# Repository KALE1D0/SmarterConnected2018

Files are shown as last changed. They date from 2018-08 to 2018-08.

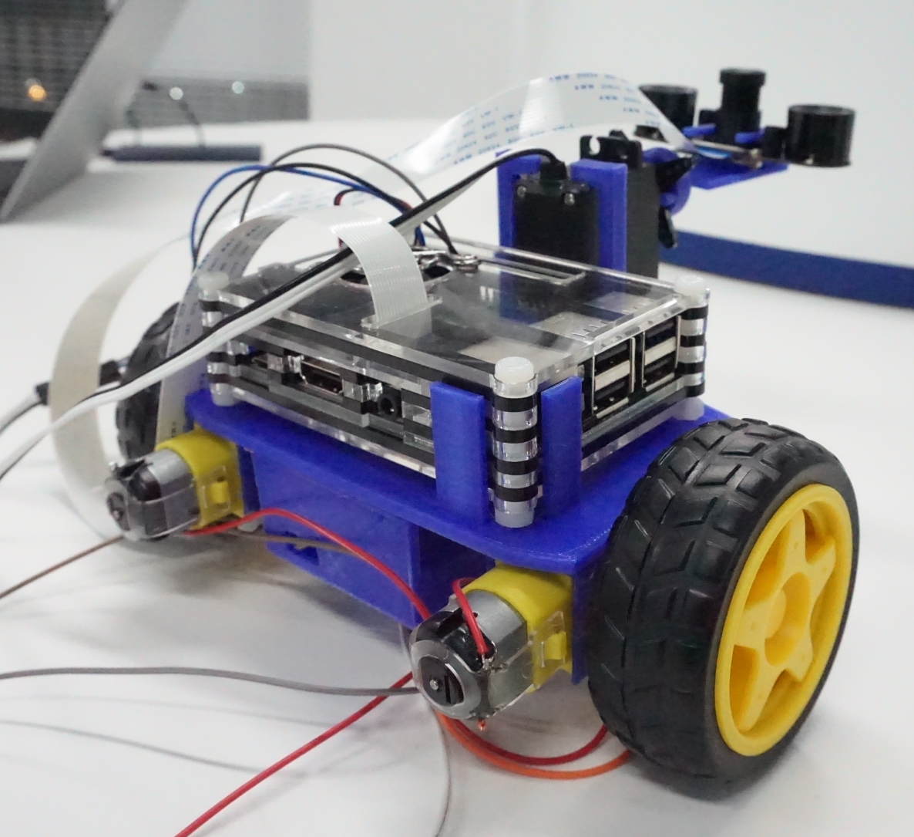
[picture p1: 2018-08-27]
photo/MKII/4.jpg

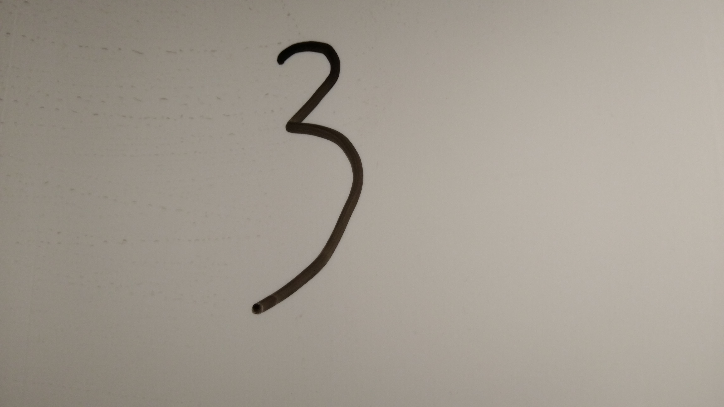
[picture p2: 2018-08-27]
src/ros_packs/znhl/picture/3.jpg

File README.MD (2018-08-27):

# What is this
A personal project cooperating with @bechanged233 and @reclugjw for Smarter-Connected-2018.

# Directories
sample\\: Test samples for defect/crack detecting.

doc\\: Reports and scripts for this project.

model\\: Solidworks model files of structure.

slide\\: PPTs for the report.

src\\: Source Codes. [src\ros_packs\send_pic] should be in the RasPi.

photo\\: Photos of our product.

# License
Copyleft.

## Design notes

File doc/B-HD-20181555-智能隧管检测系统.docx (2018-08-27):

第十四届“博创杯”全国大学生嵌入式设计大赛

作品设计报告

智能隧管检测系统

Intelligent tunnel detection system

设

计

报

告

队伍编号：

参赛学校：

作 者：

指导教师：

组 别：■本科组 □高职组

未找到目录项。

摘 要

目前的交通道路有朝着地下化、隧道化方向发展的趋势，地铁隧道也将成为未来城市交通的主要发展方向。同时各类城市管道的长度也在逐年上升。对于隧道、管道等类似的封闭环境，现有的缺陷检测方法成本高昂，形式单一，有着工序繁琐、耗时极长等弊端，不利于城市交通与管线系统的可持续发展。

因此，本项目设计了一套以图像识别与超声波测距为主要传感器，基于STM32与树莓派的小型智能化隧管缺陷检测系统，并通过ROS实现了设备与上位机的通信。我们在把对管道、隧道的缺陷检测统一化的同时，设计了一套离线作业系统，并力求在满足精确、高效的同时，将成本控制在合理的范围之内，进而使得其能够被大规模投放使用，因而具有很强的实用性与可推广性。

同时，本项目也提出了一种基于超声波传感器与摄像头相配合的小直径隧管彩色三维重构方法，并在进行数学推导与可行性论证之后，使用程序模拟实现了三维重构的效果。

关键词：智能交通、图像识别、ROS、超声波测距、三维重构

Abstract

Nowadays, the traffics system are moving toward undergroundization and tunnelling. Subways are becoming the main stream of the development of future urban transportation. At the same time, the length of various types of urban pipelines has also increased year by year. For tunnels, pipelines and similar closed environments, the existing defect detection methods are expensive, not various, and have drawbacks such as cumbersome procedures, extremely long time-consuming, and are not conducive to the sustainable development of urban traffic and pipeline systems.

Therefore, this project designed a set of small sensor tunnel detection system based on STM32 and Raspberry Pi with image recognition and ultrasonic ranging as the main sensors, and achieved communication between the device and host computer through ROS. While we unify the detection of defects in pipelines and tunnels, we designed an online operation system, and strived to control the cost within a reasonable range while satisfying the accuracy and efficiency, and in turn making it possible to be put into large-scales, so it has a strong practicality and scalability.

At the same time, a colorful 3D reconstruction method for small-diameter tunnel tubes based on ultrasonic sensors and cameras is also proposed in this project. After mathematical derivation and feasibility demonstration, the effects of 3D reconstruction are achieved using program simulation.

Key words: Intelligent traffic, image recognition, ROS, ultrasonic ranging, 3D reconstruction

第1章 绪 论

## 1.1 视觉识别技术

视觉检测系统是用相机代替人眼睛去完成识别.测量.定位等功能。一般视觉检测系统由相机、镜头、光源组合合成，可以代替人工完成条码字符 (https://baike.baidu.com/item/%E6%9D%A1%E7%A0%81%E5%AD%97%E7%AC%A6)、裂痕、包装、表面图层是否完整、凹陷等检测，使用视觉检测系统能有效的提高生产流水线的检测速度和精度，大大提高产量和质量，降低人工成本，同时防止因为人眼疲劳而产生的误判。

## 1.2 三维重构技术

三维重建，指的是通过摄像机获取场景物体的数据图像，并对此图像进行分析处理，再结合计算机视觉知识推导出现实环境中物体的三维信息。

根据重建的稀疏程度不同，可以分为以下以下几类：

稀疏重建：

通常是重建一些图像特征点的深度，这个在基于特征的视觉SLAM里比较常见，得到的特征点的深度可以用来计算相机位姿。稀疏重建在实际应用，比如检测，避障，不能满足需求。

半稠密重建：

通常是重建图像纹理或梯度比较明显的区域，这些区域特征比较鲜明。半稠密重建在直接法视觉SLAM里比较常见。重建的三维点云相对稠密，可以满足部分应用需求。

稠密重建：

稠密重建是对整个图像或者图像中的绝大部分像素进行重建。与稀疏、半稠密相比，稠密重建对场景的三维信息理解更全面，更能符合应用需求。但是，由于要重建的点云数量太多，相对耗时。本项目所设计的三维重构方法属于半稠密重建。根据重建的实时性不同，可以分为离线重建和在线重建。

离线重建：

比如 SFM(运动恢复结构)技术，此技术根据在一段时间内获得的连续图像来重建一个三维环境。

在线重建：在线重建可以分为渐进式重建和直接式重建。在线重建或多或少都和VO或者(SLAM)有联系，因为重建的时候需要相机的位姿。我们所设计的是离线重建

## 1.3 ROS机器人系统

ROS---(Robot Operating System）是一个机器人软件平台，它能为异质计算机集群提供类似操作系统的功能。ROS提供一些标准操作系统服务，例如硬件抽象，底层设备控制，常用功能实现，进程间消息以及数据包管理。ROS是基于一种图状架构，从而不同节点的进程能接受，发布，聚合各种信息（例如传感，控制，状态，规划等等）。ROS可以分成两层，低层是上面描述的操作系统层，高层则是广大用户群贡献的实现不同功能的各种软件包，例如定位绘图，行动规划，感知，模拟等等。ROS的核心是节点。节点是一小段用Python或C++写成的程序，用来执行某个相对简单的任务或进程。多个节点之间互相传递信息，并可以独立控制启动或终止。某一节点可以面向其它节点针对特定标题发布信息或提供服务。

## 1.4 隧道检测现状

随着国家经济的不断发展，为了满足日益增长的通行和城市发展需求，各类管网在近十年不断增长。据统计，截止到2017年，仅国内地铁管网长度就已经达到了世界前列，上海与北京更分列第一第二。如此大规模的交通管网带来的不仅只有方便，也带来了大量的附加问题。其中，管道维护是目前很多部门关注的重点。以地铁管道为例，现有的管道检测技术无法准确检测出管道裂缝，更无法判断出管道损坏的位置的影响程度，目前大多使用人工肉眼检测，且管道条件复杂，人工检测危险重重，国内外多次出现管道工人意外身亡事故。

第2章 系统方案

## 2.1 系统总体设计

小车端与PC主控端通过蓝牙和WIFI进行连接，开发板与PC主控端通过USB有线连接，传感器与驱动部分用串口进行连接。最终通过ROS控制各模块并且进行数据传输，从而实现预期功能。

## 2.2 系统工作流程

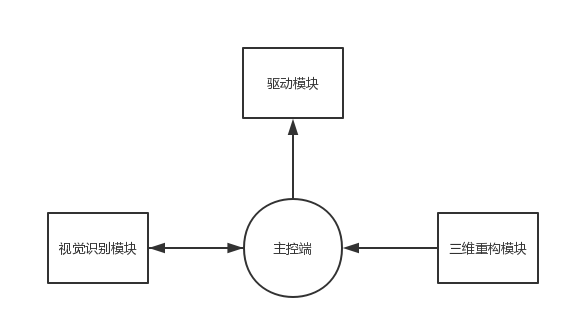
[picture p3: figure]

第3章 功能与指标

## 3.1 硬件模块

3.1.1 机械结构
1. 相机底座
相机底座采用了夹持的设计思想，通过伸出的两个臂状长方体将相机紧紧地夹在底板上，使得镜头能够在整个平面内360度旋转；同时这两个“手臂”不会影响到边上的光敏电阻与红外补光灯，使得整个设备在阴暗的环境下也能正常、平稳地工作。

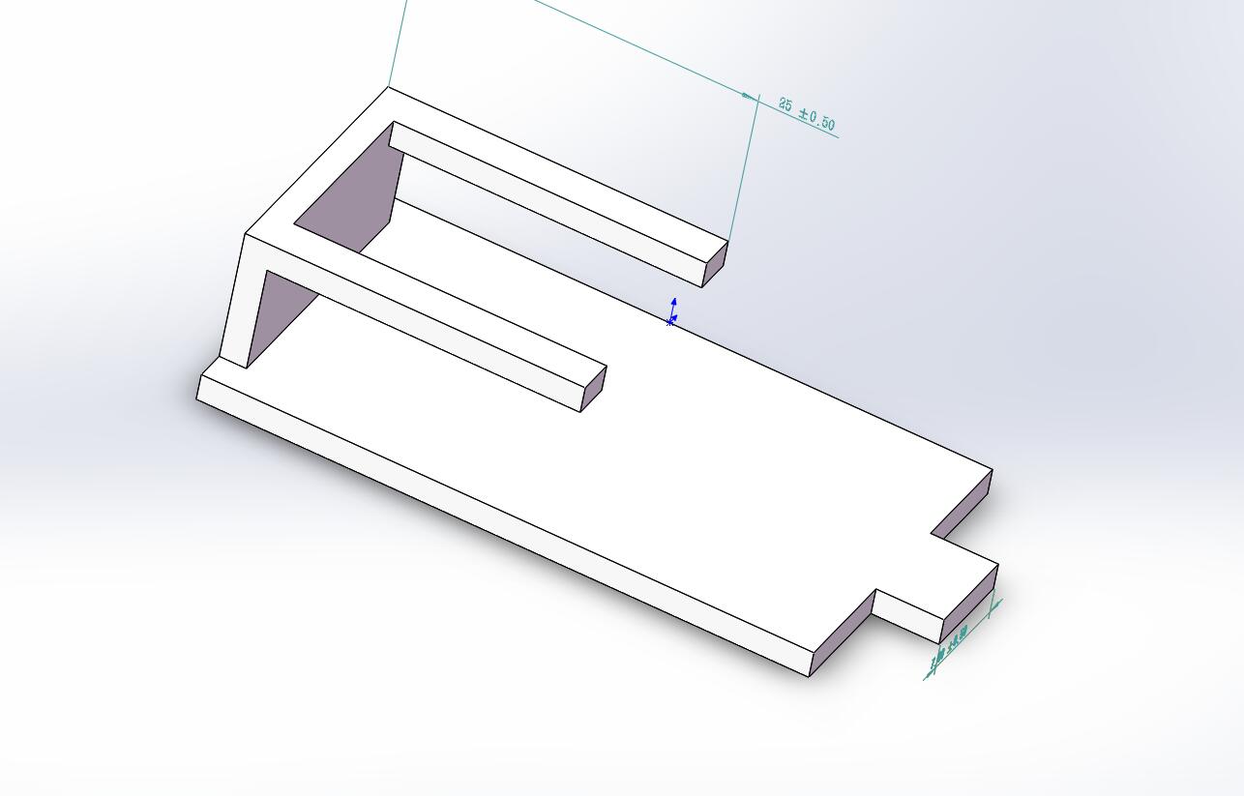
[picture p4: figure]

相机底座

2. 前部支架

前部支架为支撑车辆前部的舵机与摄像头而设计，其符合力学原理的结构与定制的万向轮插槽使得整个车辆能自由、灵活地进行转向，并能够防止车体质量的不平衡所导致的倾斜与晃动，使得车辆能够在一般环境下平稳地前进。

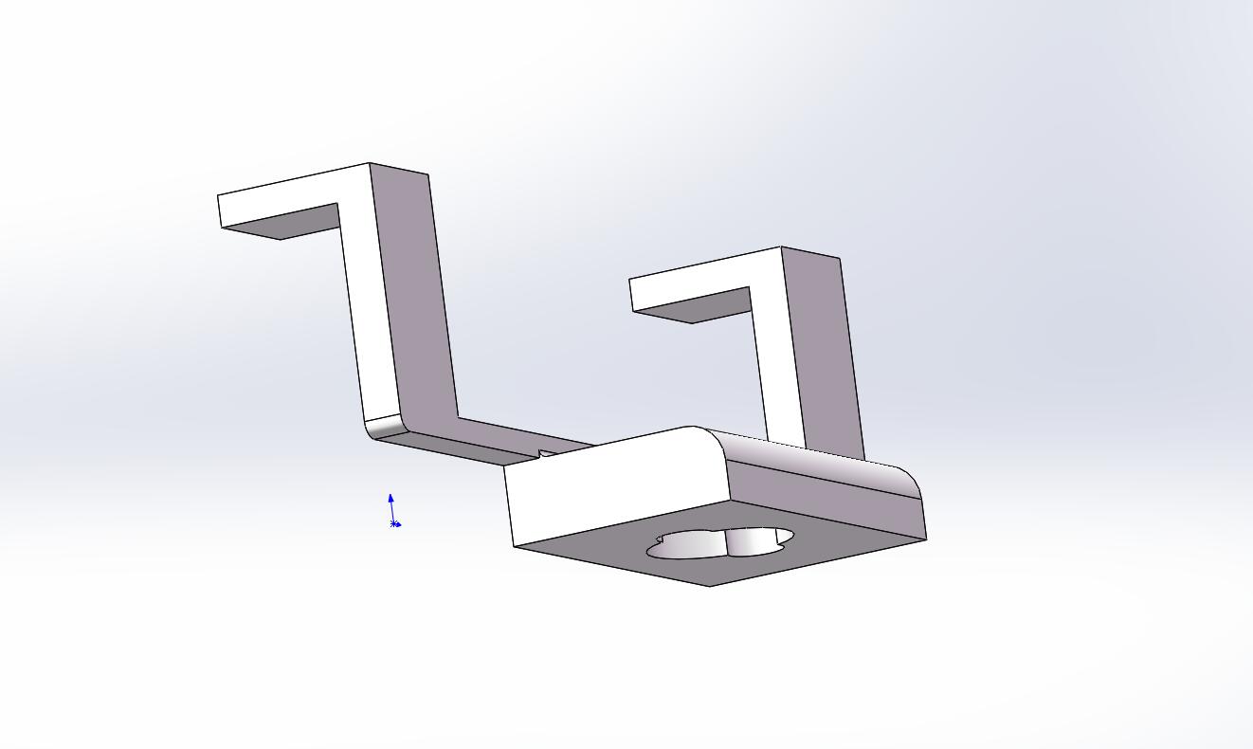
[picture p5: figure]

前置支架

3. 驱动电机支架

驱动电机支架专为直流减速电机而设计，其能够良好地对电机进行保护，并将电机的核心部件与外部环境隔离开来，有效防止电机过载等意外情况的发生。

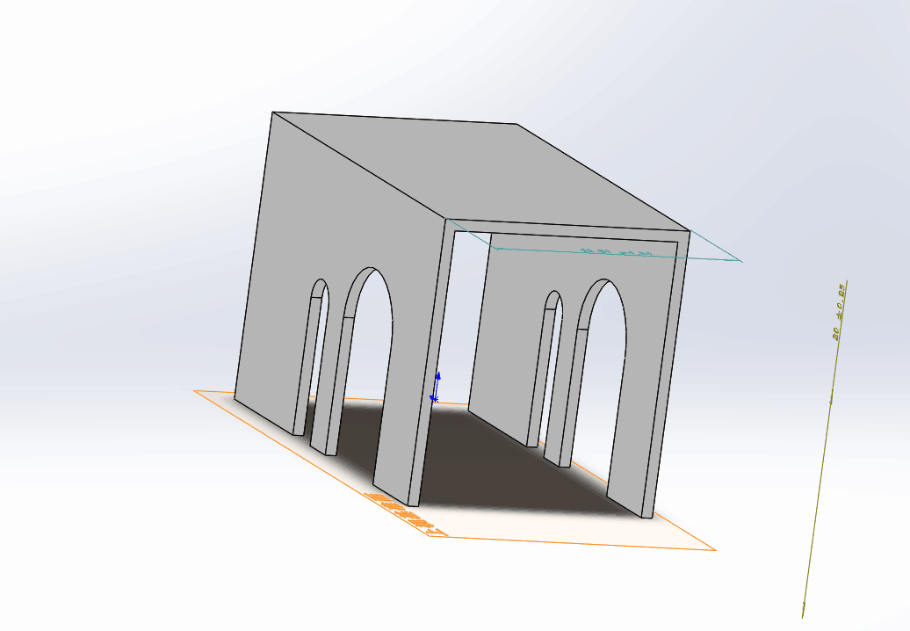
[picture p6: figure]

电机支架

4. 主控板

主控板是整个设备设计的核心，在它之下，连接了驱动电机支架与控制底座，在它中央的凹槽则是用于放置5V树莓派专用供电电池，而用保护壳进行保护的树莓派运算板则直接被放置在供电电池之上，被五个设计精巧的挡板紧紧地扣住；而在其前方，则是连接了舵机支架，进而与摄像头设备相连，使得整个系统在保证功能性的基础上将结构优化到了极致。

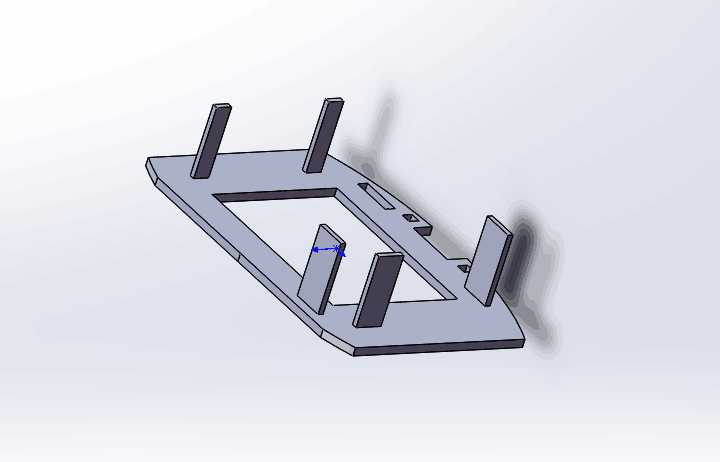
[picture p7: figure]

主控板

5. 舵机支架

舵机支架采用简单的支撑型设计，在其底部的两个圆柱向前伸出，平稳地拖住了质量较大的电机，而在支架的正下方的两个正方形凸口，则转为与主控板进行连接而设计，其能够牢牢地嵌入主控板之中，进而使得舵机能进行良好、可靠的运作。

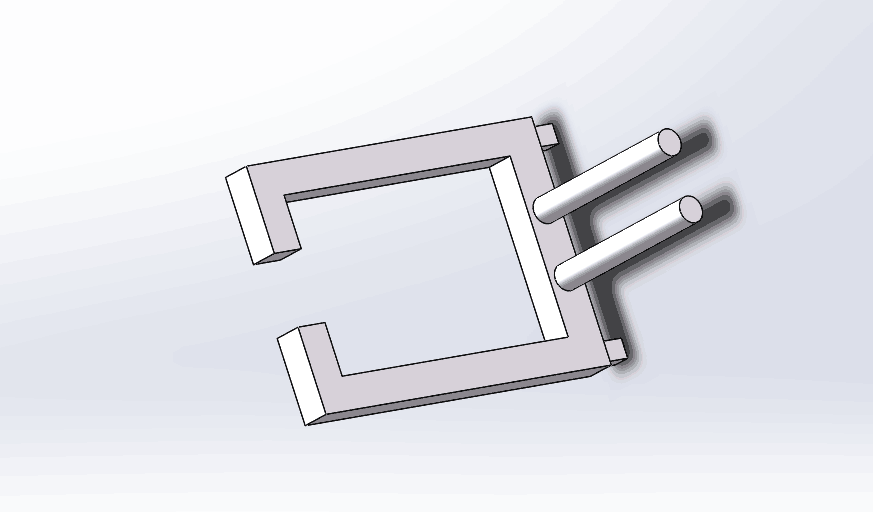
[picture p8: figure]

舵机支架

3.1.2 视觉识别硬件结构

1. Rpi Camera

我们采用带自感应式红外补光的RPiCamera摄像头。当环境光较弱时，其两侧的红外补光灯会自动开启，使得机器人能在各种不同光照环境下工作。RpiCamera的数据流可直接通过树莓派发送到上位机，从而实现实时检测的功能。

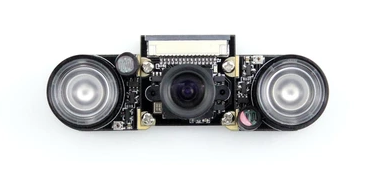
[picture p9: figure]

Rpi Camera

2. Raspberry

我们采用RaspberryPi3B来对摄像头获得的图形进行预处理与储存。RaspberryPi3B是基于ARM内核的性能强大的开源硬件，我们在其上安装了最新的轻量级操作系统Raspbian，使得我们能够非常容易地与其交互。

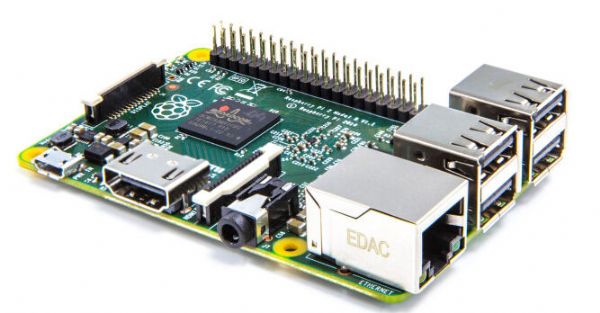
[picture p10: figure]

Raspberry Pi 3B

3.1.3. 三维重构硬件结构

我们设计的三维重构系统需要一个类似于激光雷达的传感器。我们的方案是将超声波与姿态传感器被捆绑在一起，挂载到可以三百六十度旋转的舵机上。同时，我们使用低功耗蓝牙模块来实现短距离的数据传输，使树莓派能够收到来自超声波传感器的数据。

1. 九轴姿态传感器

我们准备使用MPU9250模块来获取超声波雷达的位姿。MPU9250能够实时测量其三轴上的加速度、角加速度与地磁角，从而精确地估计出雷达的姿态角。

MPU9250

2. 超声波模块

为了提升距离的准确性，我们选用了US-100超声波传感器。US-100有着方向角较小、精度较大的特点，其探测范围可达2cm-450cm，而误差仅有0.3cm±1%，因而可以较好地检测出设备到管道内壁的距离。

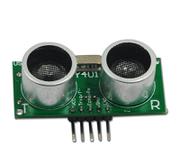
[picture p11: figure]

US-100

3.2.4. 小车运动模块硬件结构

1. STMF103C8T6

我们采用STM32F103C8T6最小系统板。STM32是基于ARM® Cortex® M 处理器内核的 32位闪存微控制器，集高性能、高实时性、数字信号处理、低功耗于一身，基于行业标准，具有大量工具和软件可供选择，是本项目控制部件的的理想选择。

STM32F103C8T6

2. 减速电机及橡胶轮

我们采用了通用减速直流电机与60mm直径的橡胶轮，其具有强磁、带抗干扰等特性。我们会为其提供5V直流供电，使得机器人能在较平缓的隧道内稳步前行。

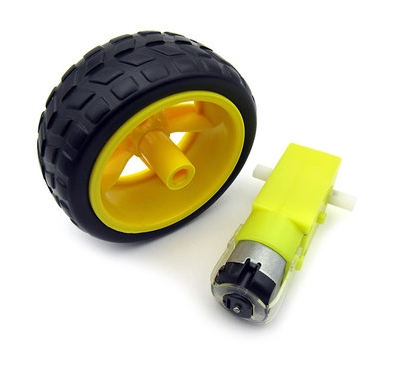
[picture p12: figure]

直流减速电机与轮胎

## 3.2 软件模块

3.2.1. 视觉识别算法

我们采用了基于视觉识别技术的缺陷检测算法，其原理是不断去除图像上的噪声，仅仅留下我们需要的特征也即裂缝等缺陷的轮廓。

1. 噪点消除

由于管道内复杂的环境与摄像头本身的物理特性，我们得到的初始图像数据往往带有较多噪点，这些噪点会影响成像的质量，进而干扰我们对缺陷特征的判断。因此，获取图像后我们首先要做的是使用滤波算法对图像去噪。

常用的滤波算法有均值滤波、高斯滤波、中值滤波等。经过我们多次尝试，在模拟的隧管环境下高斯滤波的去噪效果最好。除此之外它也有着较好的平滑化效果。

高斯滤波是一种线性平滑滤波，适用于消除高斯噪声，广泛应用于图像处理的减噪过程。通俗的说，高斯滤波就是对整幅图像进行加权平均 (https://baike.baidu.com/item/%E5%8A%A0%E6%9D%83%E5%B9%B3%E5%9D%87)的过程，每一个像素点的值，都由其本身和邻域内的其他像素值经过加权平均后得到。高斯滤波的具体操作是：用一个模板（或称卷积、掩模）扫描图像中的每一个像素，用模板确定的邻域内像素的加权平均灰度值去替代模板中心像素点的值。

高斯滤波一般有两种实现方式，一是用离散化窗口滑窗卷积，另一种通过傅里叶变换 (https://baike.baidu.com/item/%E5%82%85%E9%87%8C%E5%8F%B6%E5%8F%98%E6%8D%A2)。而只有当离散化的窗口非常大，用滑窗计算量非常大（即使用可分离滤波器的实现）的情况下，可能会考虑基于傅里叶变化的实现方法。故在这里我们使用离散化窗口滑窗卷积。

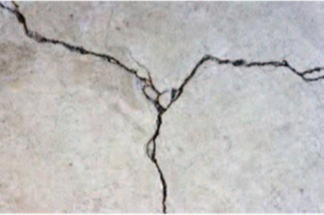
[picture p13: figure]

高斯滤波效果演示一

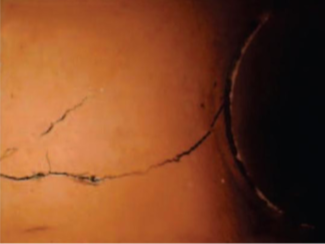
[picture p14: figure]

高斯滤波效果演示二

2. 缺陷检测：边缘检测

去除噪点之后，我们就可以对图像进行处理了。我们选用的主要缺陷检测手段是边缘检测算法。常用的边缘检测算法有Roberts算子，Sobel算子，Canny算子，形态学算子等等。

在对多种算子进行测试后，我们发现使用Canny算子进行腐蚀与膨胀运算后可以较好的检测出条状的裂缝，并且团状的潜在危险因素也能被呈现出来。

Canny算子在进行简单除噪后开始寻找图像中的亮度梯度，图像中的边缘可能会指向不同的方向，所以 Canny 算法使用 4 个 mask 检测水平、垂直以及对角线方向的边缘。原始图像与每个 mask 所作的卷积 (https://baike.baidu.com/item/%E5%8D%B7%E7%A7%AF)都存储起来。对于每个点我们都标识在这个点上的最大值以及生成的边缘的方向。这样我们就从原始图像生成了图像中每个点亮度梯度图以及亮度梯度的方向。由于较高的亮度梯度比较有可能是边缘，但是没有一个确切的值来限定多大的亮度梯度是边缘多大，所以 Canny 使用了滞后 (https://baike.baidu.com/item/%E6%BB%9E%E5%90%8E)阈值。

滞后阈值需要两个阈值——高阈值与低阈值。假设图像中的重要边缘都是连续的曲线，这样我们就可以跟踪给定曲线中模糊的部分，并且避免将没有组成曲线的噪声像素当成边缘。所以我们从一个较大的阈值开始，这将标识出我们比较确信的真实边缘，使用前面导出的方向信息，我们从这些真正的边缘开始在图像中跟踪整个的边缘。在跟踪的时候，我们使用一个较小的阈值，这样就可以跟踪曲线的模糊部分直到我们回到起点。

一旦这个过程完成，我们就得到了一个二值图像，每点表示是否是一个边缘点。进而获得我们所需要的边缘图像。

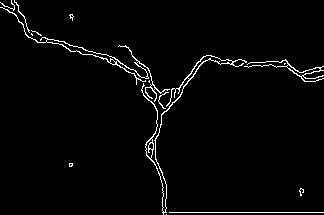
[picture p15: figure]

缺陷检测效果演示一

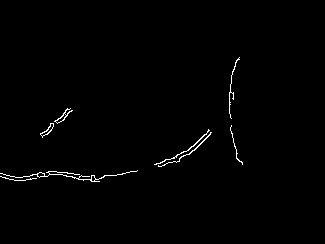
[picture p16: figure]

缺陷检测效果演示二

3. 缺陷检测：阈值分割

边缘检测算法之外，还有一类算法也能够较有效地检测出隧管壁上的缺陷，那就是阈值分割算法。阈值分割指以某一阈值为分界线将一幅图像按照灰度值转化成黑白二值图。我们将经过预处理的图像按灰度值分割成两个点集，当被分割成的两个点集之间方差最大时，该灰度值就是将图像二值化所需要的阈值。此处我们所采用的是一种自适应阈值分割算法：使用遗传算法求解的大津法(OTSU)。该方法耗时较长，可用于图像的离线处理过程之中。

使用遗传算法求解的大津法效果演示

其具体代码实现如下：

1. import cv2
2. import numpy as np
3. from matplotlib import pyplot as plt
4. import random
5. import matplotlib.patches as mpatches
6. import scipy.ndimage as ndi
7. from skimage import morphology,filters
10. imag = cv2.imread("D:test4.png")
11. cv2.imshow("orignal",imag)
13. gray = cv2.cvtColor(imag, cv2.COLOR_BGR2GRAY)
14. cv2.imshow("gray",gray)
17. img = cv2.GaussianBlur(gray,(3,3),0)
18. cv2.imshow("Gau",img)
21. canny = cv2.Canny(img, 50, 150)
22. cv2.imshow("canny",canny)
24. kernel = cv2.getStructuringElement(cv2.MORPH_RECT,(3, 3))
25. erosion = cv2.erode(img,kernel,iterations = 1)
26. dilation = cv2.dilate(erosion,kernel,iterations = 1)
27. cv2.imshow("deliation",dilation)
29. canny = cv2.Canny(dilation, 50, 150)
30. cv2.imshow("canny",canny)
31. def expand(k, m):
32. for i in list(range(len(k))):
33. k[i] = k[i][:2] + '0'*(8*m+2 - len(k[i])) + k[i][2:len(k[i])]
34. return k
37. def Hist(image):
38. a=[0]*256
39. h=image.shape[0]
40. w=image.shape[1]
41. MN=h*w
42. average=0.0
43. for i in list(range(w)):
44. for j in list(range(h)):
45. pixel=int(image[j][i])
46. a[pixel]=a[pixel]+1
47. for i in list(range(256)):
48. a[i]=a[i]/float(MN)
49. average=average+a[i]*i
50. return a, average
54. def getTh(seed, m):
55. th = [0, 256]
56. seedInt = int(seed, 2)
57. for i in list(range(0, m)):
58. tmp = seedInt & 255
59. if tmp != 0:
60. th.append(tmp)
61. seedInt = seedInt >> 8
62. th.sort()
63. return th
67. def fitness(seed, p, average, m):
68. Var = [0.0] * len(seed)
69. g_muT = 0.0
71. for i in list(range(256)):
72. g_muT = g_muT + i * p[i]
74. for i in list(range(len(seed))):
75. th = getTh(seed[i], m)
76. for j in list(range(len(th)-1)):
77. w = [0.0] * (len(th)-1)
78. muT = [0.0] * (len(th)-1)
79. mu = [0.0] * (len(th)-1)
80. for k in list(range(th[j], th[j+1])):
81. w[j] = w[j] + p[k]
82. muT[j] = muT[j] + + p[k] * k
83. if w[j] > 0:
84. mu[j] = muT[j] / w[j]
85. Var[i] = Var[i] + w[j] * pow(mu[j] - g_muT, 2)
86. return Var
90. def wheel_selection(seed, Var):
91. var = [0.0]*len(Var)
92. s = 0.0
93. n = ['']*len(seed)
94. sumV = sum(Var)
95. for i in list(range(len(Var))):
96. var[i] = Var[i]/sumV
97. for i in list(range(1, len(Var))):
98. var[i] = var[i] + var[i-1]
99. for i in list(range(len(seed))):
100. s = random.random()
101. for j in list(range(len(var))):
102. if s <= var[j]:
103. n[i] = seed[j]
104. return n
108. def Cross(Next, m):
109. for i in list(range(0, len(Next) - 1, 2)):
110. if random.random() < 0.7:
111. if m > 2:
112. tmp = Next[i][10:]
113. Next[i] = Next[i][:10] + Next[i+1][10:]
114. Next[i+1] = Next[i+1][:10] + tmp
115. else:
116. tmp = Next[i][6:]
117. Next[i] = Next[i][:6] + Next[i+1][6:]
118. Next[i+1] = Next[i+1][:6] + tmp
119. return Next
123. def Variation(Next):
124. for i in list(range(len(Next))):
125. if random.random()<0.06:
126. Next[i]=bin(int(Next[i],2)+2)
127. return Next
131. def genetic_thres(image, k, m):
132. th = image
133. for i in list(range(image.shape[0])):
134. for j in list(range(image.shape[1])):
135. for t in list(range(1, len(k)-1)):
136. if k[t-1] <= image[i][j] < k[t]:
137. th[i][j] = int(k[t-1])
138. return th
139. image=canny
140. m = 3
141. items_x = list(range(0, image.shape[0]))
142. items_y = list(range(0, image.shape[1]))
143. random.shuffle(items_x)
144. random.shuffle(items_y)
145. x = items_x[0:20*m]
146. y = items_y[0:20*m]
147. seed = []
148. Var = 0.0
149. times = 0
150. k = 0
151. P, average = Hist(image)
152. for i in list(range(0, 20)):
153. code = int(0)
154. for j in list(range(0, m)):
155. code = code + gray[x[i*j]][y[i*j]] << j*8
156. seed.append(bin(code))
158. while times < 2000:
159. Var = fitness(seed, P, average, m)
160. Next = wheel_selection(seed, Var)
161. Next = Cross(Next, m)
162. Next = expand(Variation(Next), m)
163. seed = Next
164. times = times + 1
166. for j in list(range(len(Var))):
167. if Var[j] == max(Var):
168. k = getTh(Next[j], m)
169. print (k)
171. plt.subplot(131), plt.imshow(image, "gray")
172. plt.title("source image"), plt.xticks([]), plt.yticks([])
175. plt.subplot(132), plt.hist(image.ravel(), 256)
176. plt.title("Histogram"), plt.xticks([]), plt.yticks([])
179. th1 = genetic_thres(image, k, m)
180. plt.subplot(133), plt.imshow(th1, "gray")
181. titleName = ''
182. for i in list(range(1, len(k)-1)):
183. titleName = titleName + str(k[i]) + ', '
184. titleName = titleName[:len(titleName)-2]
185. plt.title("threshold is " + titleName), plt.xticks([]), plt.yticks([])
186. plt.show()
189. cv2.waitKey(0)

3.2.2 三维重构算法

1. 倾角估测

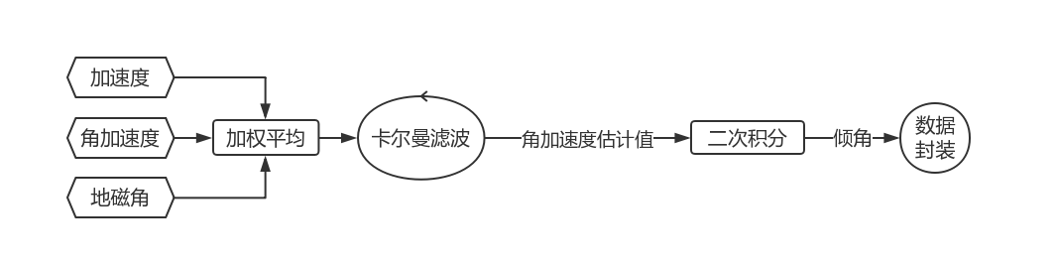
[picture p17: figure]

倾角估计算法原理

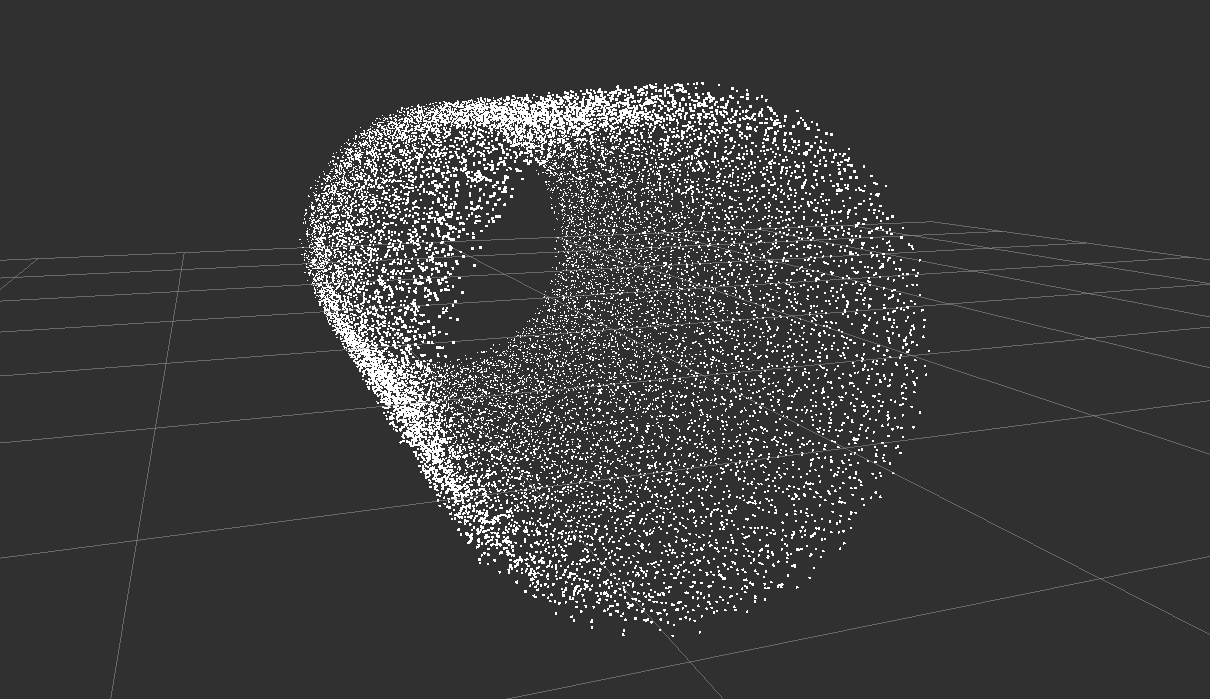
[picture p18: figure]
无标题_看图王

程序模拟的倾角估计生成的点云效果图

2. 点云染色

我们使用摄像头与超声波传感器之间的距离值L与点云到超声波传感器的距离D进行三角运算后可估算出物体在摄像机视场内与摄像机法线的夹角α，随后将其正切值与摄像机视角正切值的比例代入计算即可获得其在摄像机所获得的像素图上的具体位置，从而得到该点的像素值。

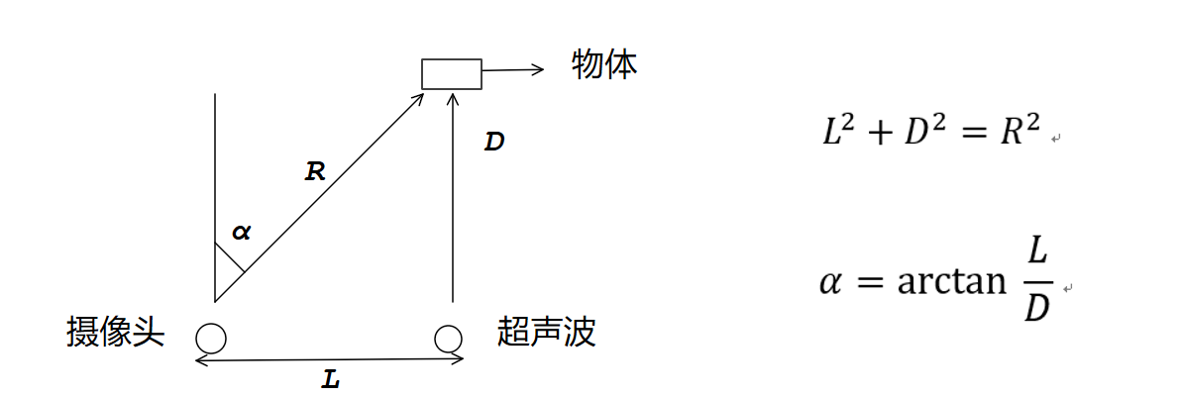
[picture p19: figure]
无标题2_看图王
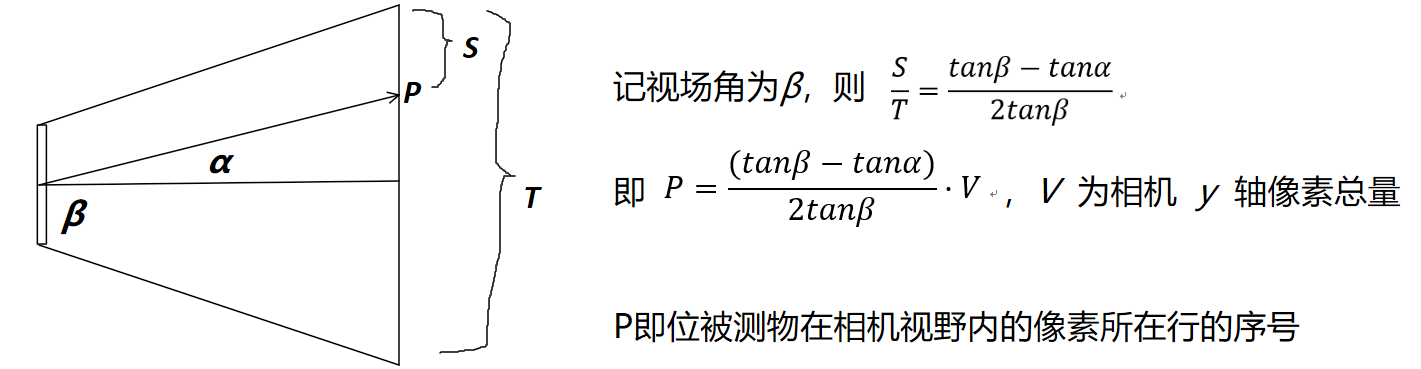
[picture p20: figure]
无标题2_看图王

点云染色算法原理

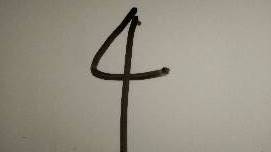
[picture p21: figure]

管道内壁数字图案实拍照片

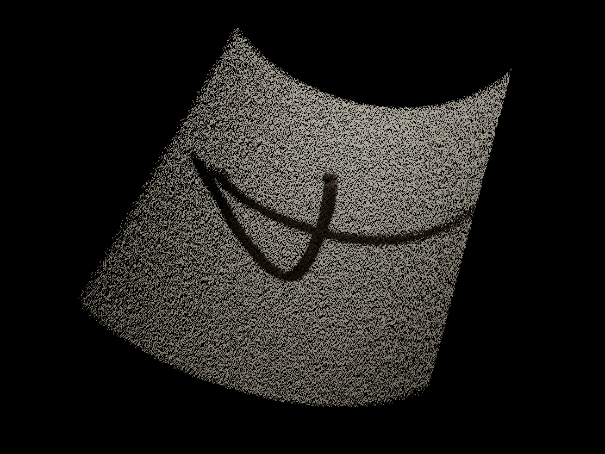
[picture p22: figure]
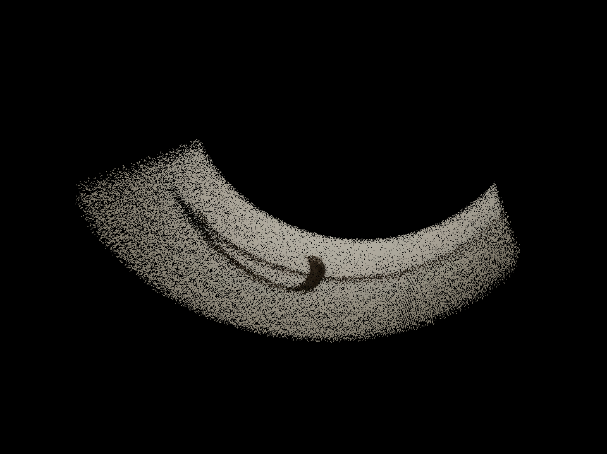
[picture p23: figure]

点云染色效果

其具体实现代码如下：

1. #include <pcl/visualization/cloud_viewer.h>
2. #include <iostream>
3. #include <pcl/io/io.h>
4. #include <pcl/io/pcd_io.h>
5. #include <opencv2/opencv.hpp>
7. using namespace std;
9. int user_data;
10. const double u0 = 319.52883;
11. const double v0 = 271.61749;
12. const double fx = 528.57523;
13. const double fy = 527.57387;
16. void viewerOneOff(pcl::visualization::PCLVisualizer& viewer)
17. {
18. viewer.setBackgroundColor(0.0, 0.0, 0.0);
19. }
21. int main()
22. {
23. pcl::PointCloud<pcl::PointXYZRGB> cloud_a;
24. pcl::PointCloud<pcl::PointXYZRGB>::Ptr cloud(new pcl::PointCloud<pcl::PointXYZRGB>);
26. cv::Mat color = cv::imread("rgb.jpg");
27. cv::Mat depth1 = cv::imread("depth.png");
29. cv::Size dsize = cv::Size(color.cols, color.rows);
30. cv::Mat depth = cv::Mat(dsize, CV_8UC3);
31. resize(depth1,depth,dsize);
33. int rowNumber = color.rows;
34. int colNumber = color.cols;
36. cloud_a.height = rowNumber;
37. cloud_a.width = colNumber;
38. cloud_a.points.resize(cloud_a.width * cloud_a.height);
40. for (unsigned int u = 0; u < rowNumber; ++u)
41. {
42. for (unsigned int v = 0; v < colNumber; ++v)
43. {
44. unsigned int num = u*colNumber + v;
45. double Xw = 0, Yw = 0, Zw = 0;
47. //Zw = ((double)depth.at<uchar>(u, v)) / 255.0 * 10001.0;
48. //Xw = (u - u0) * Zw / fx;
49. //Yw = (v - v0) * Zw / fy;
50. Zw = ((double)depth.at<uchar>(u, v));
51. Xw = u;
52. Yw = v;
54. cloud_a.points[num].b = color.at<cv::Vec3b>(u, v)[0];
55. cloud_a.points[num].g = color.at<cv::Vec3b>(u, v)[1];
56. cloud_a.points[num].r = color.at<cv::Vec3b>(u, v)[2];
58. cloud_a.points[num].x = Xw;
59. cloud_a.points[num].y = Yw;
60. cloud_a.points[num].z = Zw;
61. }
62. }
64. *cloud = cloud_a;
66. pcl::visualization::CloudViewer viewer("Cloud Viewer");/*
67. viewer.showCloud(cloud);
69. viewer.runOnVisualizationThreadOnce(viewerOneOff);
71. while (!viewer.wasStopped())
72. {
73. user_data = 9;
74. }
75. */
76. return 0;
77. }

3. 三维重构

通过将获得的彩色点云数据打包封装成ROS消息发布到ROS系统里，让RVIZ对其进行监听与处理，即可在RVIZ中看到彩色的三维重构结果。

其具体实现代码如下：

1. #include <ros/ros.h>
2. #include <pcl/point_cloud.h>
3. #include <pcl_conversions/pcl_conversions.h>
4. #include <sensor_msgs/PointCloud2.h>
5. #include <bits/stdc++.h>
7. pcl::PointCloud<pcl::PointXYZ> gen_pipe(int round, int layer, int length) {
8. pcl::PointCloud<pcl::PointXYZ> cloud;
9. cloud.width = round * layer;
10. cloud.height = 1;
11. cloud.points.resize(cloud.width * cloud.height);
13. for (size_t i = 0; i < cloud.points.size (); ++i)
14. {
15. double theta = (double)(i % round) / round * 2 * acos(-1.0);
16. cloud.points[i].x = (double)(i / round + 1) / layer * length;
17. cloud.points[i].y = cos(theta) * (1 + rand () / (RAND_MAX + 1.0f) / 7);
18. cloud.points[i].z = sin(theta) * (1 + rand () / (RAND_MAX + 1.0f) / 7);
19. }
20. return cloud;
21. }
23. main (int argc, char **argv)
24. {
25. ros::init (argc, argv, "pcl_create");
27. ros::NodeHandle nh;
28. ros::Publisher pcl_pub = nh.advertise<sensor_msgs::PointCloud2> ("pcl_output", 1);
29. //pcl::PointCloud<pcl::PointXYZ> cloud = gen_circle();
30. sensor_msgs::PointCloud2 output;
31. //Convert the cloud to ROS message
32. ros::Rate loop_rate(1);
33. while (ros::ok())
34. {
35. pcl::toROSMsg(gen_pipe(200, 100, 5), output);
36. output.header.frame_id = "world";
37. pcl_pub.publish(output);
39. ros::spinOnce();
40. loop_rate.sleep();
41. }
43. return 0;
44. }

第4章 实现原理

第5章 系统框图

## 5.1 硬件框图

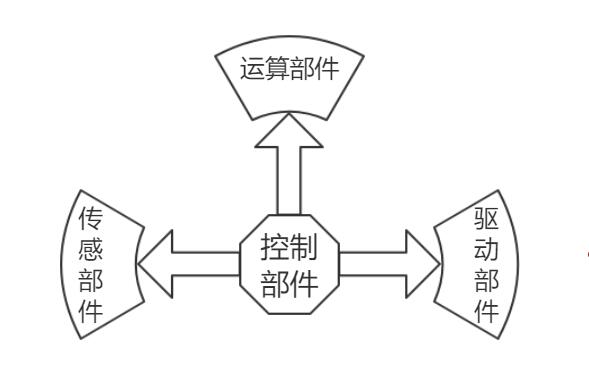
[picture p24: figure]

## 5.2 软件框图

5.2.1 控制系统

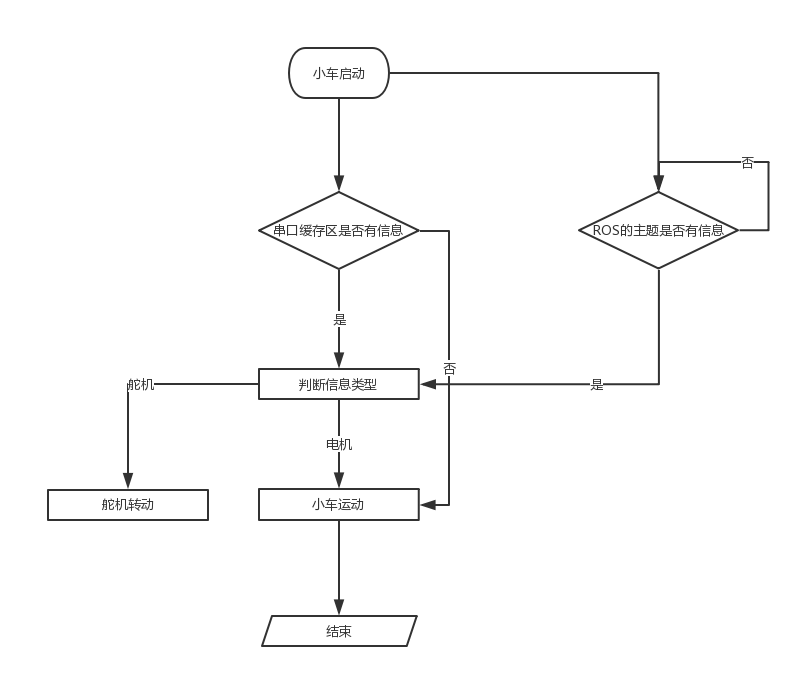
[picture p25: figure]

控制系统框图

5.2.2 视觉识别与三维重构框图

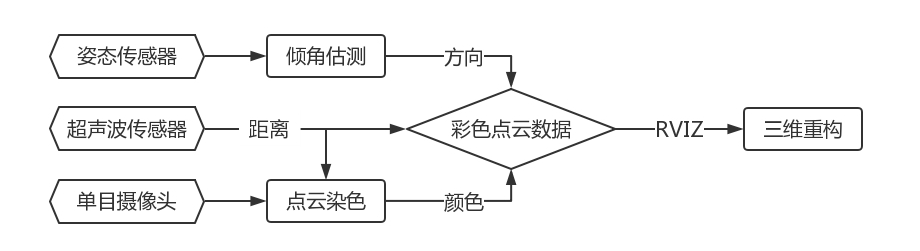
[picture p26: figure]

第6章 测试方案

## 6.1 硬件相关配置

PC端：接入主路由，连接魔法师平台开发板，通过USB对Arduino和STM32进行调试与程序烧录。

树莓派：连接电源，接入WIFI，接好与Rpi Camera的连线以及与Arduino的连线。

Arduino：接入电源，插好排线。

## 6.2 软件相关配置

PC端：打开实现配置好的含有ROS的Ubuntu虚拟机，启动ROS Core，记录ROS Core地址，打开Rviz，待命。

树莓派：修改配置为PC端ROS Core地址，启动ROS Core，启动主Node。

## 6.3 具体测试流程

1. PC端发送前进命令，测试在隧道内行进的流畅性和准确性。
2. PC端发送停止命令，之后发送检测命令，测试在静止环境下摄像头拍摄的清晰度以及检测的准确性和完整性。
3. PC端发送前进命令，测试在行进状态下检测的准确性和三维重构的准确性及速度。
4. 重复上述操作，直到达到预期状态为止。

## 6.4 结果分析

我们对小车前进的稳定性和检测的准确性进行了测试。

我们的小车在接受ROS发送的前进命令后，能够在较短时间内启动，并且在直行隧道内保持稳定速度直线前行，小车未出现大的车身振动，目视车身没有结构损坏。在弯道上，小车能够原地准确的转弯，进入下一隧道，准确性满足行进需求。

我们的摄像头在接受ROS发送的检测命令后，在静止环境下，摄像头转动频率稳定，Rviz传输的图像清晰，处理后的图像准确。在行进过程中，摄像头转动仍然能保持稳定，图像的清晰度未受大的影响，处理后图片仍满足设计要求。

综上，我们小车已初步具备预期的隧道检测的能力

第7章 特色

本项目的产品的硬件与相关算法均为自主设计，拥有很强的适应性与可扩展性，因而将能够面对复杂多变的各类隧管环境。且本项目的设备在其设计之初便预留较多的工业接口，可以安装多个特征传感器，从而实现“一次检测多种管道，一遍查出多种问题”，填补了此类产品的市场空白。

本项目已实现的管道缺陷检测方法主要依赖于对单目摄像头的图像进行处理，在成本和准确度上进行了取舍，有较强的可移植性和可扩展性。同时我们也采用了由现代生物进化论启发的遗传算法，从而能够使找到全局最优解的可能性大大增加。此外，通过边缘检测与阈值分割两种算法的配合，我们的检测方法能够较好的适应光照不均匀的情况，从而减少检测过程中产生的误差。

本项目提出了一种基于超声波的低成本三维重构思路，并实现了相关算法。该方案将能对管道内的环境进行较好的呈现。

本项目采用了分布式机器人操作系统ROS作为主体框架。ROS具有硬件抽象、底层设备控制、进程间与跨进程通信以及程序包管理等诸多功能，是时下新兴的智能机器人控制方案。我们实现了从STM32与树莓派端进行数据收集，随后发送至PC端进行处理，再经过PC端的数据处理与分析，将具体指令反馈给树莓派端的控制回路，从而实现了对机器设备进行精准合理的控制以及对数据的快速传输与储存。

本项目将定制的跨平台的设备管理程序，以实现快速、准确的管道问题检测，并且能精准定位问题管道区域所在位置。未来还将提供依托设备管理软件提供的集群操作功能，单个工作人员即可完成大面积城市隧管网络检测工作，从而极大地减少了人力成本。

第8章 应用前景

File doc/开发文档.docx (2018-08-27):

1、 开发目的
a) 城市地下管网建设成本大，其检修清洁问题更成了令人头疼的一大难题。现有的方法主要是利用管道检测仪。该方法工序繁琐、成本高昂、工程量大、所需人工极多。
b) 为了解决这一问题，真正意义上做到科技发展为人类生产生活做出贡献，本项目设计了一款基于树莓派的管道检伤机器人。其在具有自主智能化强、工作量小等优点的同时，将成本控制在了一个非常合理的范围内，具有很强的实用性与可推广性。
2、 项目思路及技术细节
  a) 在小车结构方面，由于城市地下管网不同于普通平地地面，管壁具有弧度，普通轮式小车或者履带式小车不能在管道内稳定前进，且管道转角处空间小，转弯难度极高，为此我们采用XX轮，该轮具有较大的与管壁之间的摩擦力，能使小车平稳前进，小车车身使用了正方形设计，尽可能减小车身面积与降低小车重心，使得小车在转角处能顺利转弯，自身状态也能保持稳定。
  b) 在控制器方面，项目采用了基于ARM平台的树莓派作为主控制板。该平台具有功耗低，运算速度较快的特点，使得小车能进行复杂操作。为了在保证系统稳定性与可靠性的同时尽可能地加快运算速度以及降低系统功耗，我们选取了ubuntu-mate操作系统,且使用PC端的UBUNTU16.04系统进行控制。
  c) 在控制平台方面，为了对机器设备进行精准合理的控制，项目采用了基于分布式的进程框架的机器人软件平台ROS。ROS具有硬件抽象、底层设备控制、常用功能实现、进程间消息以及数据包管理等诸多功能，是时下新兴的智能机器人控制方案。小车利用树莓派端进行数据收集，并发送至PC端进行处理，再经过PC端的数据处理与分析，将具体指令反馈给树莓派端，从而实现对小车的有效控制以及对数据的充分分析。
  d) 在传感器方面，受体积与资金限制，样机仅装备了激光雷达作为简易探伤设备，并加入和超声波传感器。依靠激光雷达和超声波传感器，利用测距算法和SLAM技术，我们能精确定位小车位置和探测管道状态，且能准确定位漏洞位置，初步估计漏洞大小以及影响程度，为管道修复提供参考。另外，本平台预留了多路工业标准4～20mA数据接口、串行数据UART、RS232、RS485等接口，同时预留多路AD转换端口与数字IO口，以便于各类不同传感器的扩展，使用者只需要在连接相应传感器接口，并在本机器人的人机接口或相关软件进行简单设置即可完成新增传感器的部署。故本项目具有极强的适应性与可扩展性。
3、 项目主要用途、适用范围以及价值
a) 项目可以广泛运用于现代生产生活中的各种城市地下管网，为载体管道提供故障检测等服务。
b) 通过预留的多路工业标准数据接口，使用方可以快速、便捷地扩展各种通用接口传感器设备，加之以SLAM技术，使得产品具有了极强的环境适应性与可扩展性，可以广泛运用于各种条件下的管道环境，尤其是对燃气管道和输油管道等高危管道进行检测，。
c) 相比于传统的城市地下管网检测仪，本项目在工程量、工序、成本等方面做出了极大的突破。与此同时，将成本控制在了一个非常合理的范围内，具有很强的实用性与可推广性。

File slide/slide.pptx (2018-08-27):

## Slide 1

智能隧管检测系统

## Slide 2

目录

项目背景
应用前景
作品设计
创新点和困难点

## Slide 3

项目背景

成本

安全

效率

DSC01802_看图王

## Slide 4

总体构架

管理人员

PC

RasPi

双向通信

图像


减速电机

RPICAMERA

基于STM32自主设计的控制板

控制

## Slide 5

结构设计


3D打印

DSC01802_看图王

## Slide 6


控制系统程图

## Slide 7

图象识别：预处理


灰度化

腐蚀膨胀

原图

滤波

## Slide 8

图象识别：识别与标注


边缘检测
（Canny算子）


识别与标注

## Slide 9

三维重构

H5蓝牙模块


STM32F103

超声波模块

距离

姿态

九轴姿态传感器

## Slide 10

三维重构：倾角检测

无标题_看图王

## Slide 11

三维重构：点云染色

无标题2_看图王
无标题2_看图王

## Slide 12

创新点和困难点

自主设计的软硬件结构
高效清晰的图像识别算法
基于超声波的低成本三维重构方案
以分布式机器人操作系统ROS作为主体框架，可以方便地升级为分布式协作系统

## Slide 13

应用场景

大规模检伤
需要的操作人员少，设备成本低，设备操作难度低，适合被大规模投放使用。
快速定位
设备检测反应快速，结果准确，适合对隧管内的缺陷进行快速定位。
隧管维护
未来将制作与设备配合的App控制程序，进一步提升其隧管维护的易用性。

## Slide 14

实物照片


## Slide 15

谢谢

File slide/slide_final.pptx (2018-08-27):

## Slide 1

智能隧管检测系统

威力加强版

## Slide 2

目录

项目背景
应用前景
作品设计
创新点和困难点

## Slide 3

项目背景

初代机

成本

安全

效率

DSC01802_看图王

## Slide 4

总体构架

控制与运算

Raspberry Pi

基于STM32的集成电路控制板

双向通信

管理人员

PC/Android

传感器

RPICAMERA

图像

驱动器

减速直流电机

控制

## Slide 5

结构设计

3D打印

DSC01802_看图王

更坚固，更稳定

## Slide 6

控制系统程图


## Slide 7

图象识别：预处理

原图


灰度化

滤波

腐蚀膨胀

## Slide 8

图象识别：识别与标注


边缘检测
（Canny算子）

识别与标注

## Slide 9

图象识别：可视化的改进


（新增功能）


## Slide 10

图象识别效果展示


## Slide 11

图象识别效果展示


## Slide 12

图象识别效果展示


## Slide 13

图象识别效果展示


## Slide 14

三维重现

H5蓝牙模块

STM32F103

超声波模块

距离

姿态

九轴姿态传感器

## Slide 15

三维重现：倾角检测

无标题_看图王

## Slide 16

三维重现：点云染色

无标题2_看图王
无标题2_看图王

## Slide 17

创新点和困难点

自主设计且经过多次迭代的程序与硬件结构
稳定高效清晰直观的缺陷识别检测算法
基于超声波的低成本三维重现方案
结构组件与模块性价比高且较耐用
总体架构基于ROS，可以升级为分布式协作系统

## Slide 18

应用场景

大规模检伤
需要的操作人员少，设备成本低，设备操作难度低，适合被大规模投放使用。
快速定位
设备检测反应快速，结果准确，适合对隧管内的缺陷进行快速定位。
隧管维护
未来将制作与设备配合的App控制程序，进一步提升其隧管维护的易用性。

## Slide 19

实物照片


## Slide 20

谢谢

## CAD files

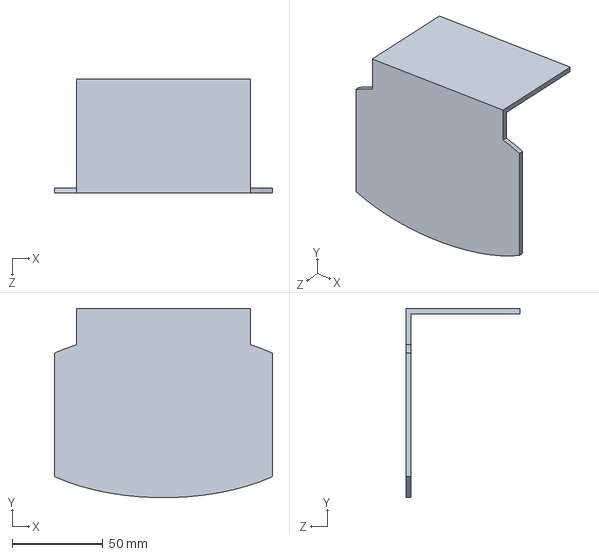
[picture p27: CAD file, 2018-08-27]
model/BottomMainboard.SLDPRT
120.0 x 104.2 x 63.0 mm

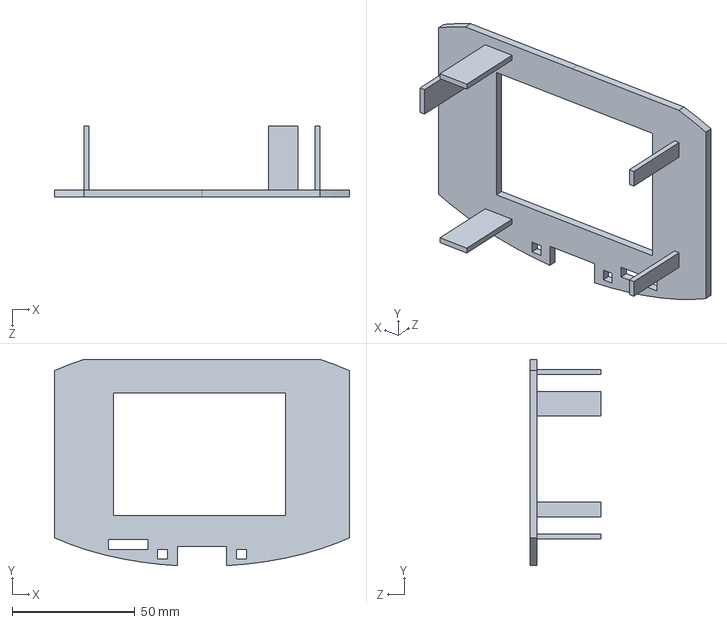
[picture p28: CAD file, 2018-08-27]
model/Mainboard.SLDPRT
120.0 x 83.9 x 29.0 mm

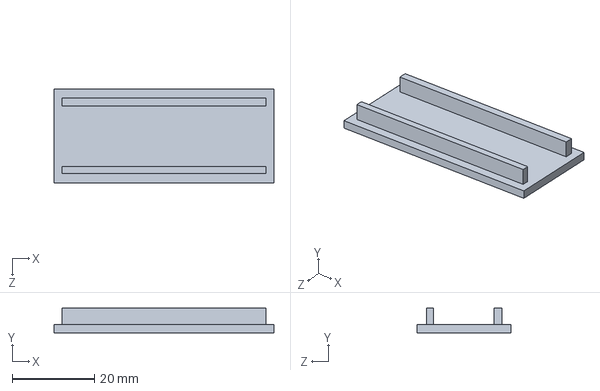
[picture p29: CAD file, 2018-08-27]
model/module/stm32.SLDPRT
53.3 x 6.00 x 22.9 mm

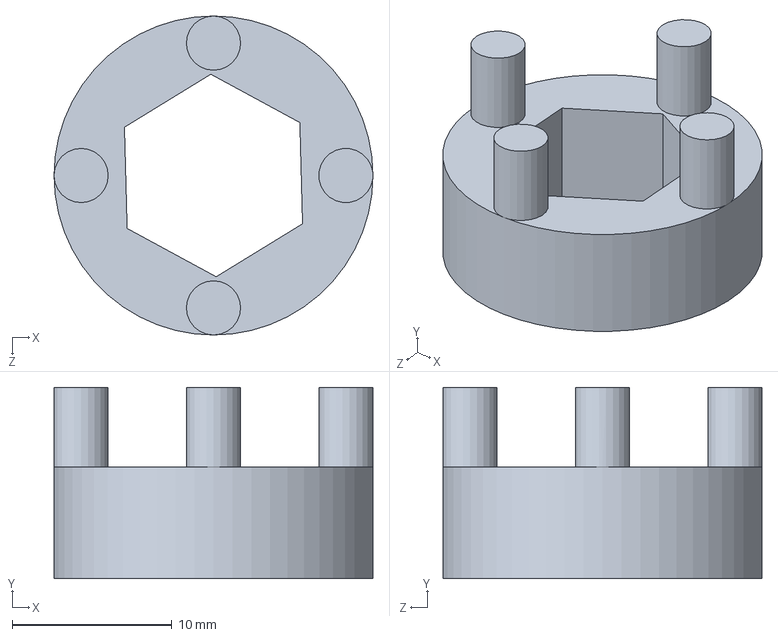
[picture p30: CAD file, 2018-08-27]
model/trans1.SLDPRT
20.0 x 12.0 x 20.0 mm

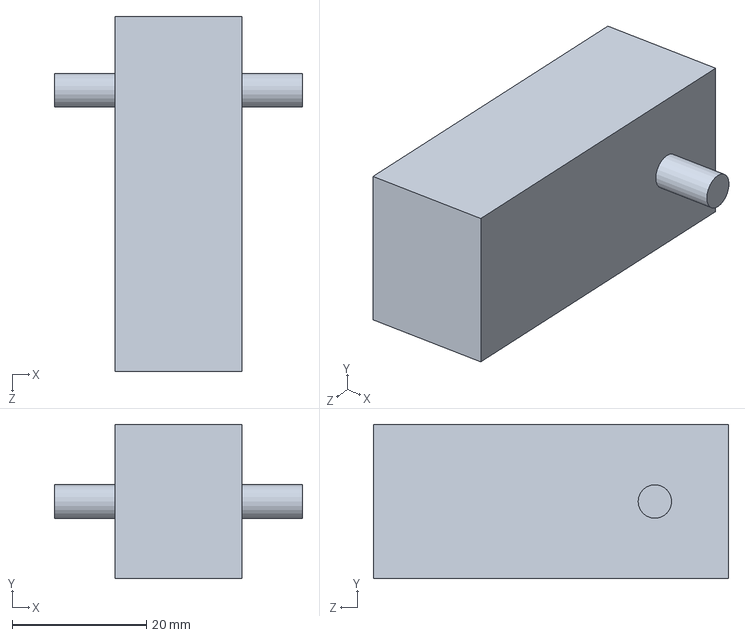
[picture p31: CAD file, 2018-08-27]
model/module/driver.SLDPRT
37.0 x 23.0 x 53.0 mm

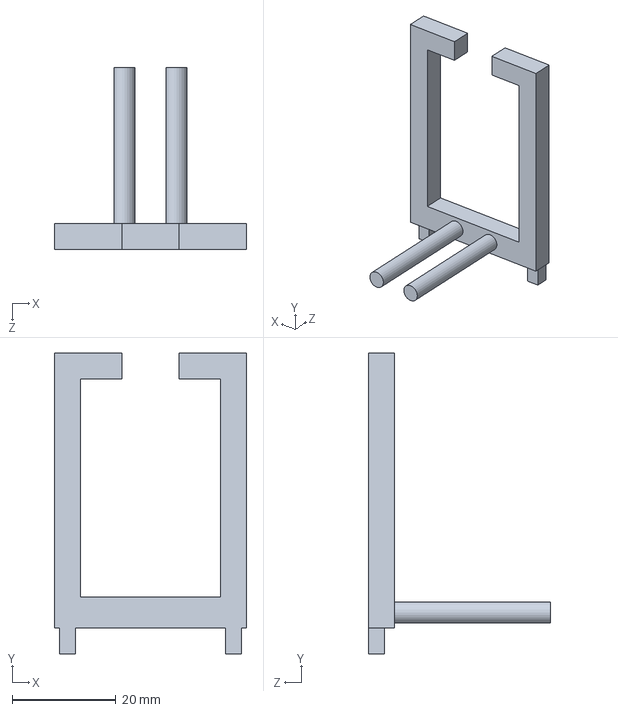
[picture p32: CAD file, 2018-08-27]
model/SteeringShelf.SLDPRT
37.0 x 58.0 x 35.0 mm

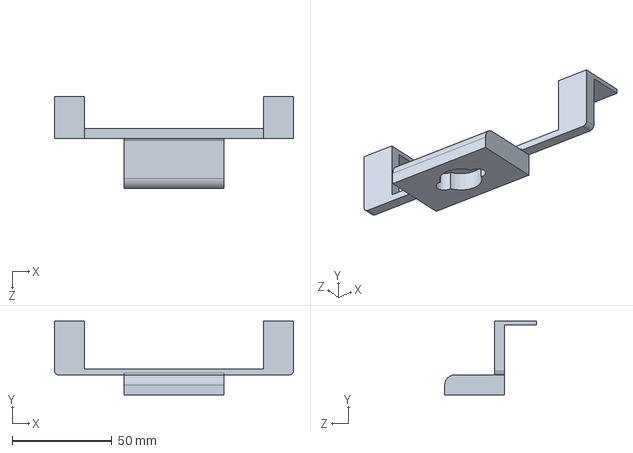
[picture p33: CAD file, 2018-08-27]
model/DirectionShelf.SLDPRT
120.0 x 37.0 x 46.0 mm

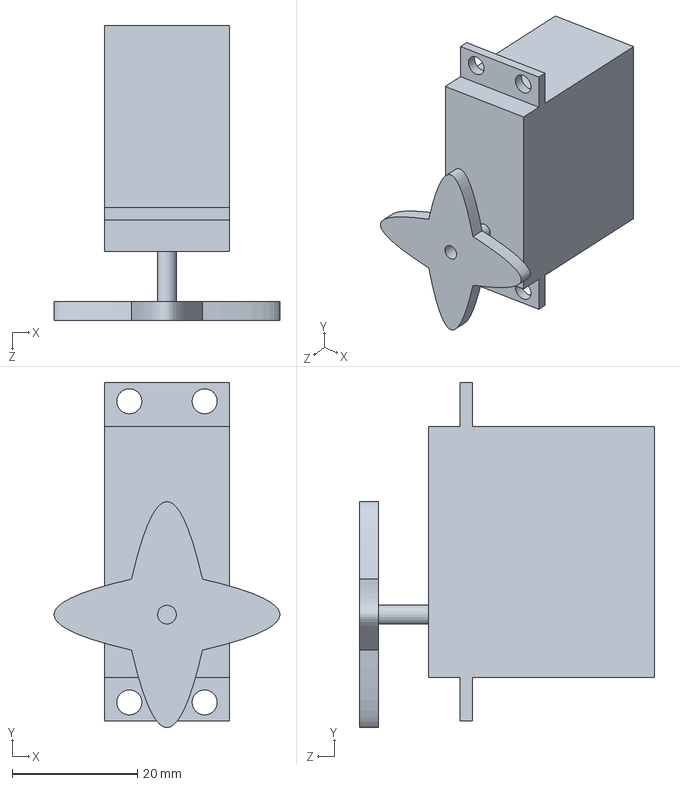
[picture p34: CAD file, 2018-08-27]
model/module/steer.SLDPRT
36.0 x 55.0 x 47.0 mm

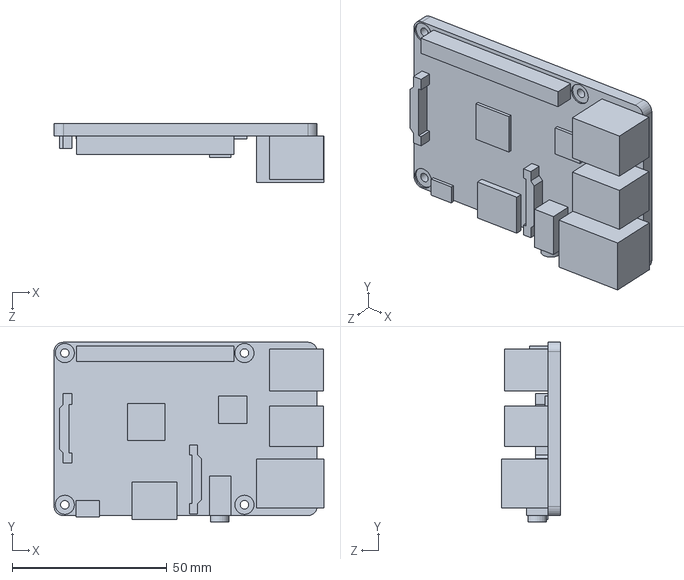
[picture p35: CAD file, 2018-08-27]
model/module/raspi.SLDPRT
87.2 x 58.0 x 19.0 mm

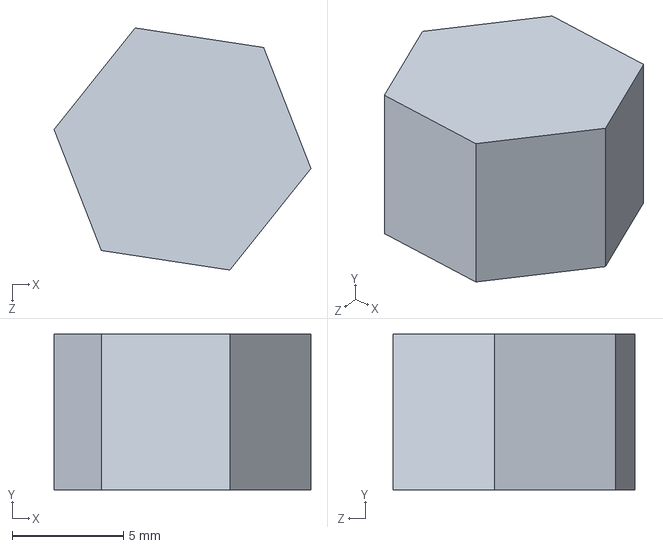
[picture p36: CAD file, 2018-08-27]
model/trans2.SLDPRT
11.5 x 7.00 x 10.9 mm

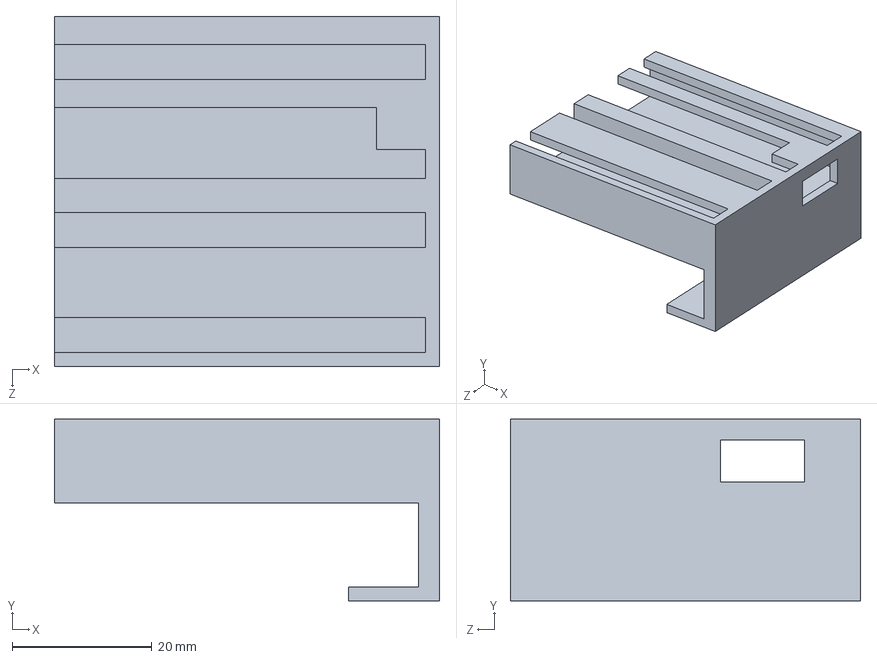
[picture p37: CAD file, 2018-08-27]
model/ControlShelf.SLDPRT
55.0 x 26.0 x 50.0 mm

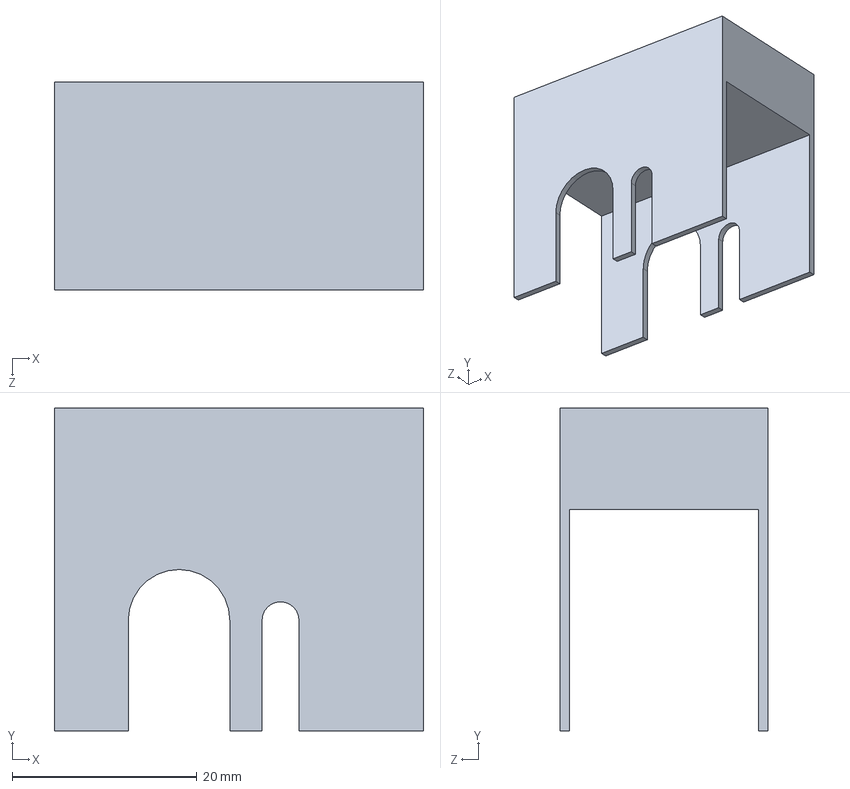
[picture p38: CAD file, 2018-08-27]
model/DriverShelf.SLDPRT
40.0 x 35.0 x 22.5 mm

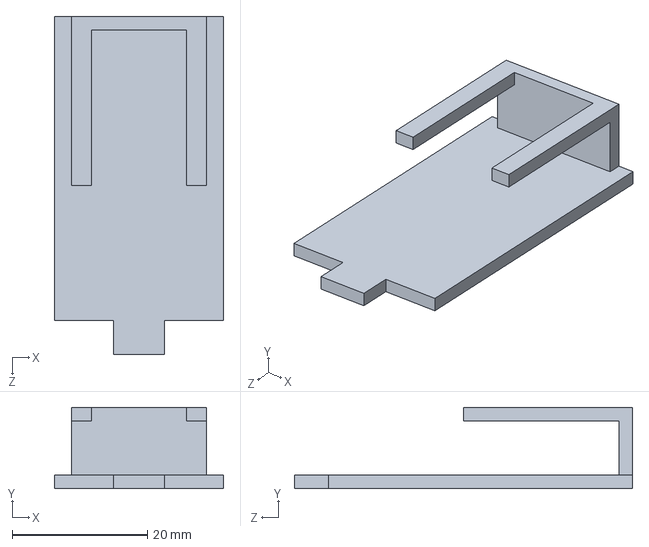
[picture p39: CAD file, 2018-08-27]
model/CameraShelf.SLDPRT
25.0 x 12.0 x 50.0 mm

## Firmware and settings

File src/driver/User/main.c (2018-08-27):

/******************** (C) COPYRIGHT 2012 WildFire Team **************************
 * 文件名  ：main.c
**********************************************************************************/
#include "stm32f10x.h"
#include "led.h"
#include "key.h"
#include "usart.h"
#include "motor.h"
//#include "SysTick.h"
//#include "timer.h"
//#include "UltrasonicWave.h"
u8 u8BluetoothValue;
void delay(vu32 nCount)
{
  for(; nCount != 0; nCount--);
}

int main(void)
{	
	 //u8 KeyNum = 0;
//	u8 u8BluetoothValue;
	//SystemInit();                   //=====系统初始化
//	Timerx_Init(5000,7199);				   //定时器TIM1
//	UltrasonicWave_Configuration(); 	   //超声波初始化设置 IO口及中断设置		
	/* LED 端口初始化 */
	//LED_GPIO_Config();
	//GPIO_KEY_Config();
	USART1_Config();
	USART3_Config();
	NVIC_Configuration();
	TIM2_PWM_Init();
	MOTOR_GPIO_Config();
  TIM_SetCompare3(TIM2,50);
	TIM_SetCompare4(TIM2,50);
	
	//GPIO_SetBits(GPIOB, GPIO_Pin_13);
	GPIO_SetBits(GPIOB, GPIO_Pin_13 | GPIO_Pin_15);GPIO_SetBits(GPIOB, GPIO_Pin_12 | GPIO_Pin_14); 
	//GPIO_SetBits(GPIOB, GPIO_Pin_11 | GPIO_Pin_12| GPIO_Pin_14| GPIO_Pin_15);
	//LED1( ON );
	while (1)
	{
			
	}
}
	

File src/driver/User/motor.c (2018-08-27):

#include "stm32f10x.h"
#include "motor.h"
//#define ENCODER_TIM_PERIOD (u16)0xFFFF
//#define MAX_COUNT          (u16)0x0FFF
/*
  控制GPIO PB12/PB13/PB14/PB15
  MOTOR  TIM2_CH3/TIM2_CH4
  编码器 TIM3_CH1/TIM3_CH2
  编码器 TIM4_CH1/TIM4_CH2
*/

void MOTOR_GPIO_Config(void)
{		
	/*定义一个GPIO_InitTypeDef类型的结构体*/
	GPIO_InitTypeDef GPIO_InitStructure;

	/*开启GPIOB的外设时钟*/
	RCC_APB2PeriphClockCmd(RCC_APB2Periph_GPIOB, ENABLE); 

	/*选择要控制的GPIOB引脚*/															   
  	GPIO_InitStructure.GPIO_Pin = GPIO_Pin_12 | GPIO_Pin_13 | GPIO_Pin_14 | GPIO_Pin_15;	

	/*设置引脚模式为通用推挽输出*/
  	GPIO_InitStructure.GPIO_Mode = GPIO_Mode_Out_PP;   

	/*设置引脚速率为50MHz */   
  	GPIO_InitStructure.GPIO_Speed = GPIO_Speed_50MHz; 

	/*调用库函数，初始化GPIOB*/
  	GPIO_Init(GPIOB, &GPIO_InitStructure);		  

	/* 低电平	*/
	GPIO_SetBits(GPIOB, GPIO_Pin_13 | GPIO_Pin_14|GPIO_Pin_12 | GPIO_Pin_15);
	//GPIO_SetBits(GPIOB, GPIO_Pin_13 | GPIO_Pin_14);
	//GPIO_ResetBits(GPIOB, GPIO_Pin_12 | GPIO_Pin_15);	 
}

/*
 * 函数名：TIM2_GPIO_Config
 * 描述  ：配置TIM3复用输出PWM时用到的I/O
 * 输入  ：无
 * 输出  ：无
 * 调用  ：内部调用
 */
static void TIM2_GPIO_Config(void) 
{
  GPIO_InitTypeDef GPIO_InitStructure;

	/* TIM2 clock enable */
	//PCLK1经过2倍频后作为TIM2的时钟源等于72MHz
  RCC_APB1PeriphClockCmd(RCC_APB1Periph_TIM2, ENABLE); 

  /* GPIOA clock enable */
  RCC_APB2PeriphClockCmd(RCC_APB2Periph_GPIOA, ENABLE); 

  /*GPIOA Configuration: TIM2 channel 3 and 4 as alternate function push-pull */
  GPIO_InitStructure.GPIO_Pin =  GPIO_Pin_2 | GPIO_Pin_3;
  GPIO_InitStructure.GPIO_Mode = GPIO_Mode_AF_PP;		    // 复用推挽输出
  GPIO_InitStructure.GPIO_Speed = GPIO_Speed_50MHz;

  GPIO_Init(GPIOA, &GPIO_InitStructure);

}

/*
 * 函数名：TIM2_Mode_Config
 * 描述  ：配置TIM3输出的PWM信号的模式，如周期、极性、占空比
 * 输入  ：无
 * 输出  ：无
 * 调用  ：内部调用
 */
static void TIM2_Mode_Config(void)
{
	TIM_TimeBaseInitTypeDef  TIM_TimeBaseStructure;
	TIM_OCInitTypeDef  TIM_OCInitStructure;

	/* PWM信号电平跳变值 */
	//u16 CCR1_Val = 500;        
	//u16 CCR2_Val = 800;
	u16 CCR3_Val = 0;
	u16 CCR4_Val = 0;
	//u16 PrescalerValue;
/* -----------------------------------------------------------------------
    TIM2 Configuration: generate 4 PWM signals with 4 different duty cycles:
    TIM3CLK = 72 MHz, Prescaler = 0x0, TIM3 counter clock = 72 MHz
    TIM3 ARR Register = 71999 => TIM3 Frequency = TIM3 counter clock/(ARR + 1)
    TIM3 Frequency = 1 KHz.
	CC1 update rate = TIM2 counter clock / CCR1_Val
    TIM3 Channelx duty cycle = (TIM2_CCRx/ TIM2_ARR)* 100 = x%
    
  ----------------------------------------------------------------------- */

  /* Time base configuration */		 
  TIM_TimeBaseStructure.TIM_Period = 255;       //当定时器从0计数到999，即为1000次，为一个定时周期
  TIM_TimeBaseStructure.TIM_Prescaler = 3;	    //设置预分频：不预分频，即为72MHz
  TIM_TimeBaseStructure.TIM_ClockDivision = TIM_CKD_DIV1 ;	//设置时钟分频系数：不分频
  TIM_TimeBaseStructure.TIM_CounterMode = TIM_CounterMode_Up;  //向上计数模式

  TIM_TimeBaseInit(TIM2, &TIM_TimeBaseStructure);

  /* PWM2 Mode configuration: Channel3 */
  TIM_OCInitStructure.TIM_OCMode = TIM_OCMode_PWM1;	    //配置为PWM模式1
  TIM_OCInitStructure.TIM_OutputState = TIM_OutputState_Enable;	
  TIM_OCInitStructure.TIM_Pulse = CCR3_Val;	   //设置跳变值，当计数器计数到这个值时，电平发生跳变
  TIM_OCInitStructure.TIM_OCPolarity = TIM_OCPolarity_High;  //当定时器计数值小于CCR1_Val时为高电平

  TIM_OC3Init(TIM2, &TIM_OCInitStructure);	 //使能通道2

  TIM_OC3PreloadConfig(TIM2, TIM_OCPreload_Enable);

  /* PWM1 Mode configuration: Channel4 */
  TIM_OCInitStructure.TIM_OutputState = TIM_OutputState_Enable;
  TIM_OCInitStructure.TIM_Pulse = CCR4_Val;	  //设置通道2的电平跳变值，输出另外一个占空比的PWM

  TIM_OC4Init(TIM2, &TIM_OCInitStructure);	  //使能通道3
  TIM_OC4PreloadConfig(TIM2, TIM_OCPreload_Enable);

  TIM_ARRPreloadConfig(TIM2, ENABLE);			 // 使能TIM3重载寄存器ARR

  /* TIM2 enable counter */
  TIM_Cmd(TIM2, ENABLE);                   //使能定时器2	
}

/*
 * 函数名：TIM2_PWM_Init
 * 描述  ：TIM2 输出PWM信号初始化，只要调用这个函数
 *         TIM3的四个通道就会有PWM信号输出
 * 输入  ：无
 * 输出  ：无
 * 调用  ：外部调用
 */
void TIM2_PWM_CHANGE(u16 CCR3,u16 CCR4)
{
	TIM_OCInitTypeDef  TIM_OCInitStructure;
	u16 CCR3_Val ;
	u16 CCR4_Val ;
	CCR3_Val = CCR3;
	CCR4_Val =CCR4;
	TIM_OCInitStructure.TIM_OCMode = TIM_OCMode_PWM1;	    //配置为PWM模式1
  TIM_OCInitStructure.TIM_OutputState = TIM_OutputState_Enable;	
  TIM_OCInitStructure.TIM_Pulse = CCR3_Val;	   //设置跳变值，当计数器计数到这个值时，电平发生跳变
  TIM_OCInitStructure.TIM_OCPolarity = TIM_OCPolarity_High;  //当定时器计数值小于CCR1_Val时为高电平

  TIM_OC3Init(TIM2, &TIM_OCInitStructure);	 //使能通道2

  TIM_OC3PreloadConfig(TIM2, TIM_OCPreload_Enable);

  /* PWM1 Mode configuration: Channel4 */
  TIM_OCInitStructure.TIM_OutputState = TIM_OutputState_Enable;
  TIM_OCInitStructure.TIM_Pulse = CCR4_Val;	  //设置通道2的电平跳变值，输出另外一个占空比的PWM

  TIM_OC4Init(TIM2, &TIM_OCInitStructure);	  //使能通道3
  TIM_OC4PreloadConfig(TIM2, TIM_OCPreload_Enable);
}
void TIM2_PWM_Init(void)
{
	TIM2_GPIO_Config();
	TIM2_Mode_Config();	
}
